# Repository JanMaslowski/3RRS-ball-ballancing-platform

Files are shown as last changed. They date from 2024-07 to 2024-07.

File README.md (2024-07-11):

# 3RRS-ball-ballancing-platform

This repository contains everything needed to create a 3RRS manipulator capable of controlling a ball on a platform using a camera and a PID controller. Programs for the Raspberry Pi 4B are written in Python, and there is also a MATLAB simulation of the model's reverse kinematics. This project was developed as my bachelor thesis and successfully defended at WUST in 2024.

Short video of constructed robot : https://youtu.be/mO_4qzWjOGI

<p align="center">
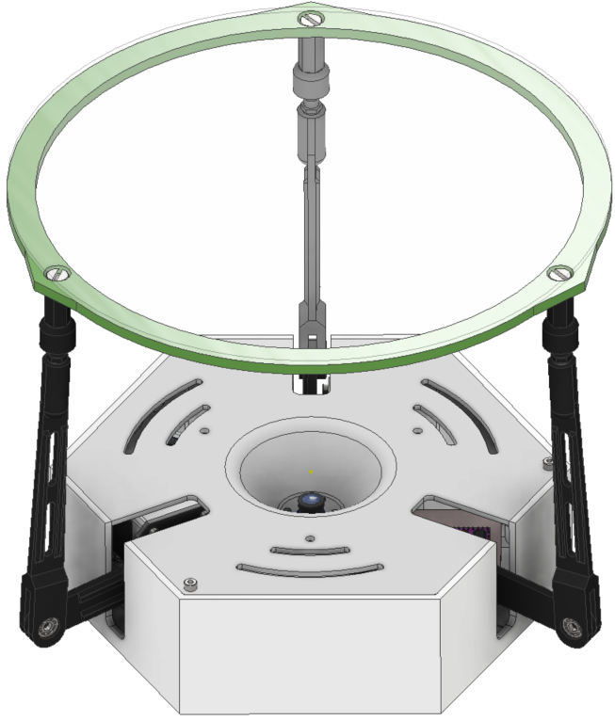
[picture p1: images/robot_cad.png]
Robot CAD
  
</p>

The project shown above was created in Inventor. All files essential for building this robot can be found in the `/inventor_parts_and_model` directory, and the STL files are located in the `/STL_models` directory. Parts that are not included in these directories, such as ball joints or the plexiglass top, were purchased instead of 3D printed. 
On the pictures below you can see parts used to create the robot:

<p align="center">
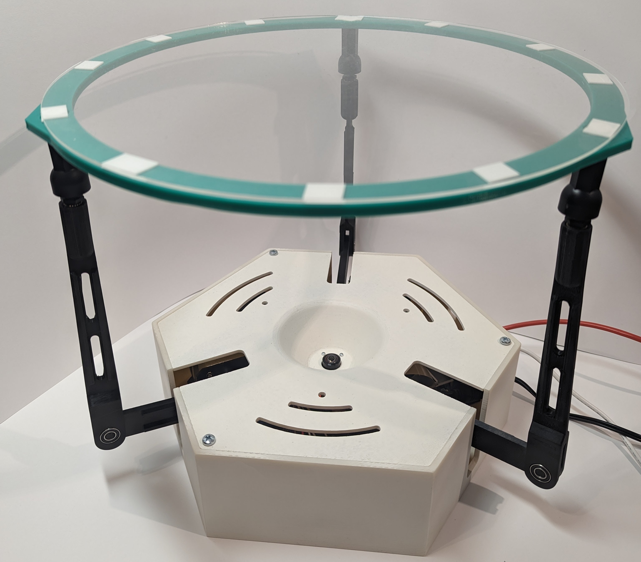
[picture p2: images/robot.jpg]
Robot CAD
  
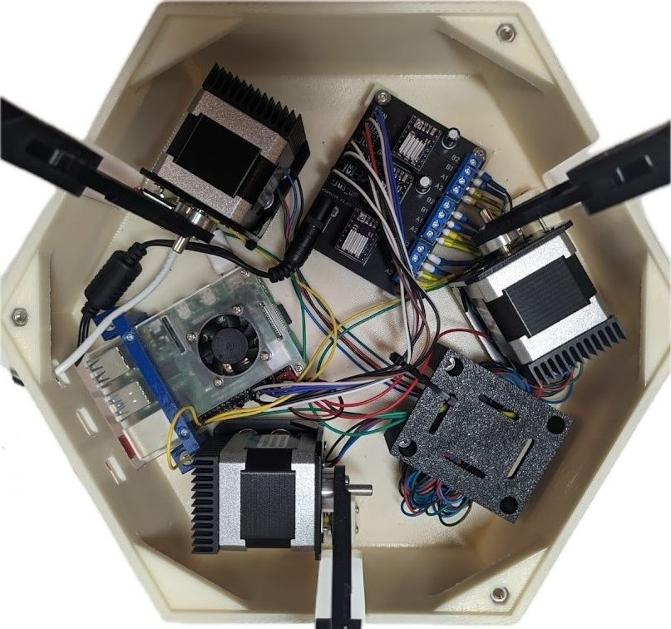
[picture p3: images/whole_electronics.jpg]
Another Image
  
</p>

- Raspberry pi 4b 8GB RAM
- DRV8825 stepper motor driver
- JK42HS40-0404 200 steps 12V/0,4A/0,4Nm stepper motor
- HD M OV5647 5Mpx Camera (fisheye lens)

 PCB board was designed for this project, and its schematic can be found in the `images` directory.

## Matlab simulation

The `simulation.m` file contains a visualization of the platform's circular movement. It helps to understand how inverse kinematics works by analyzing movements with different parameters.

## Camera calibration

A wide-angle camera was used to lower the construction and set everything inside one box. This caused significant image distortion. To manage this, the `/camera_calibration` directory contains two files. The first one, `calibrate.py`, helps to find the camera matrices needed to undistort images. To find these values, you should take photos of a chessboard and put them into the same directory before running the script. The second file, `undistort.py`, shows the image after the undistortion procedure and should be run with the command `undistort.py image_name`.

<p align="center">
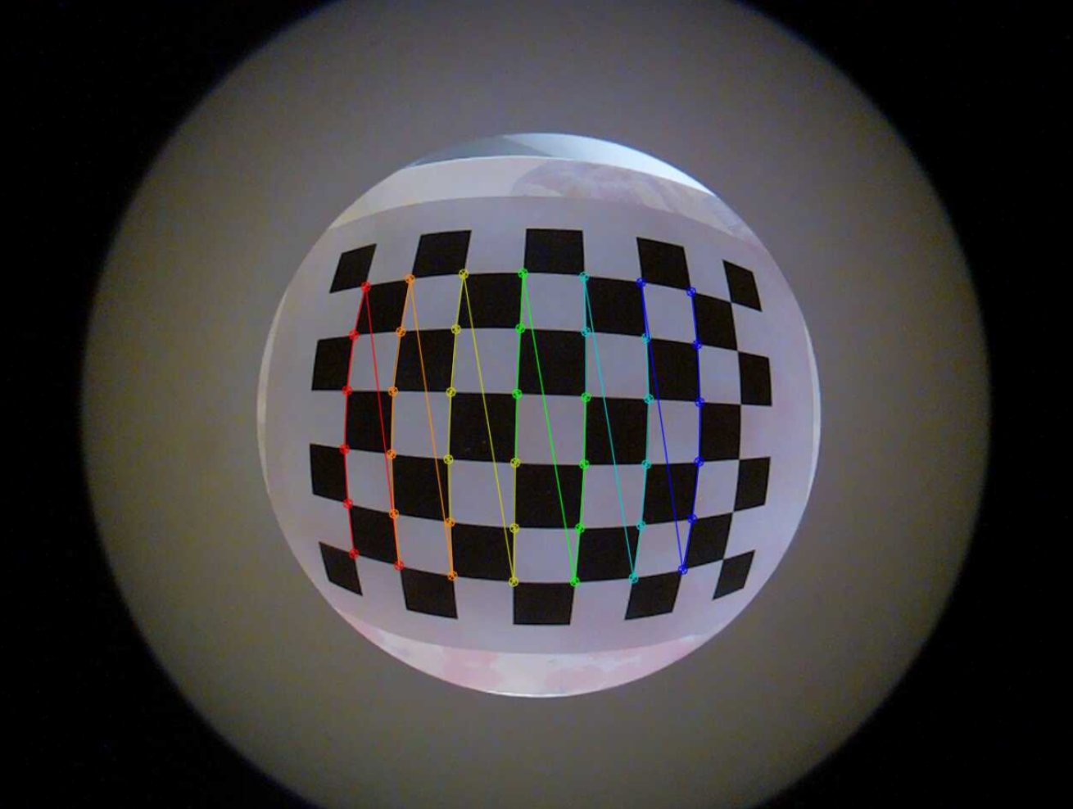
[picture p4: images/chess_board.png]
Robot CA7D
  
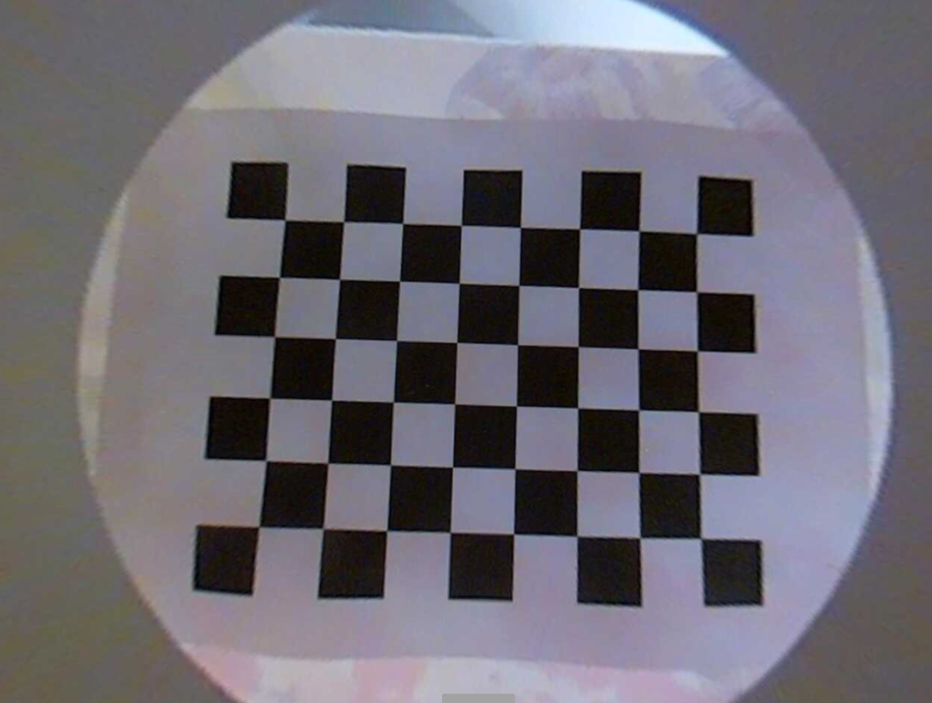
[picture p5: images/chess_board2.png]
Another Ima7ge
  
</p>
Images befor and after camera calibration.

## Scripts

The `scripts` directory contains all the scripts needed to run the platform. Each file is responsible for different functions, which are composed in the `main.py` function.

- `calc.py` is responsible for calculating the inverse kinematics of the manipulator.
- `camera.py` handles all detection tasks, such as finding the ball or the center of the platform. These functionalities are shown in the pictures below.

<p align="center">
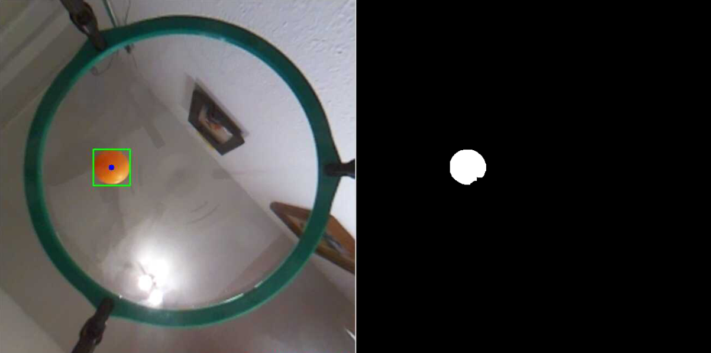
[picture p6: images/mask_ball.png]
Ball Detection
  
</p>

<p align="center">
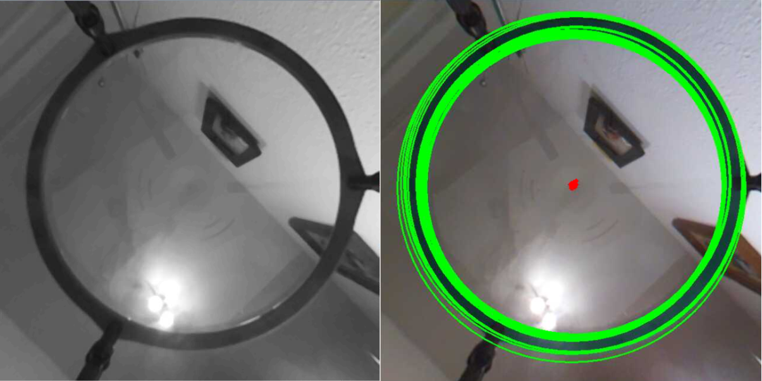
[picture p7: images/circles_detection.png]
Platform Center Detection
  
</p>

- `move32.py` manages all robot movements, such as setting the ground position parallel to the base and reating for ball movement.
- `pid.py` contains the PID regulator algorithm.
- `main.py` sets everything up and runs the program. To see a live view of the camera, as shown below, you should run `main.py --show-trajectory`.

<p align="center">
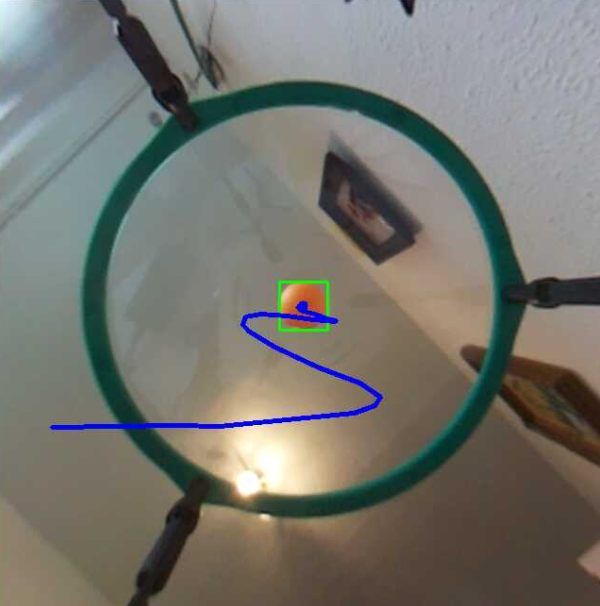
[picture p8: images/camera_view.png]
Camera View
  
</p>

## Other information

Because of the fisheye lens and significant image distortion, the Raspberry Pi 4B 8GB manages to run the program at about 15 frames per second. To increase FPS, ARM NEON and ARM VFPV3 technologies were used. For projects of this kind, you should consider using at least a Raspberry Pi 5 if a fisheye lens is used. It is also likely that this program can be optimized for better performance.

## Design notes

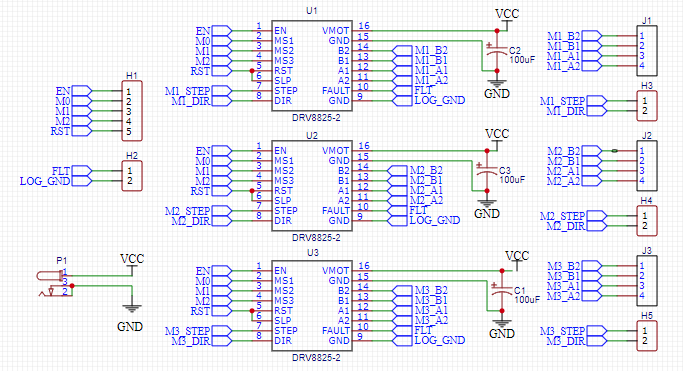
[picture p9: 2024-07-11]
images/pcb_project.png

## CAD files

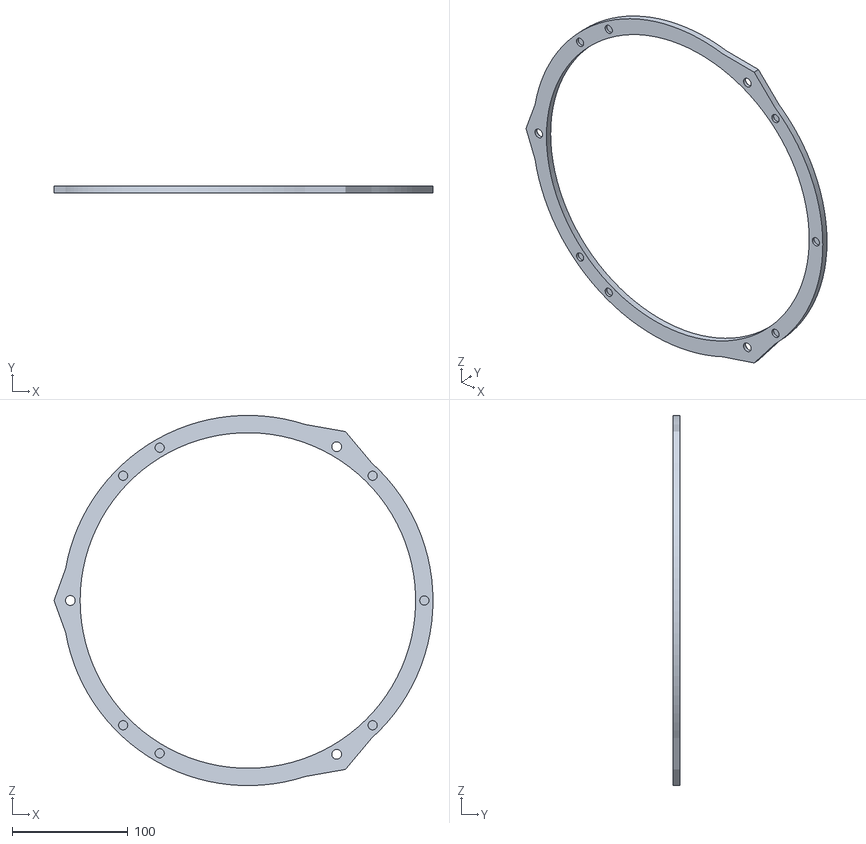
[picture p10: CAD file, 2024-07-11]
STL_models/top.stl
327.6 x 6.00 x 319.9

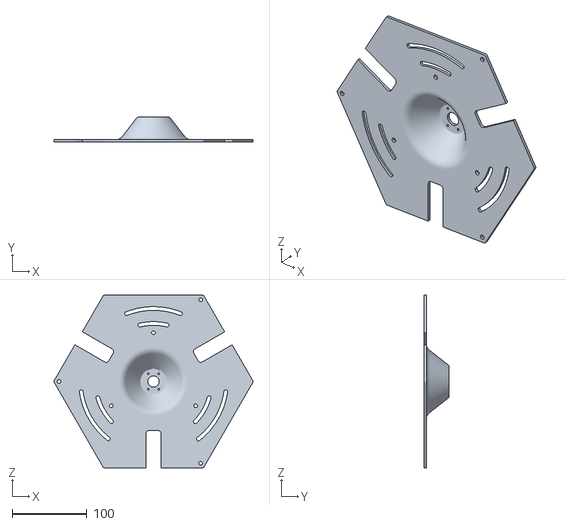
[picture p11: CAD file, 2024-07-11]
STL_models/base_cover.stl
265.8 x 33.0 x 231.0

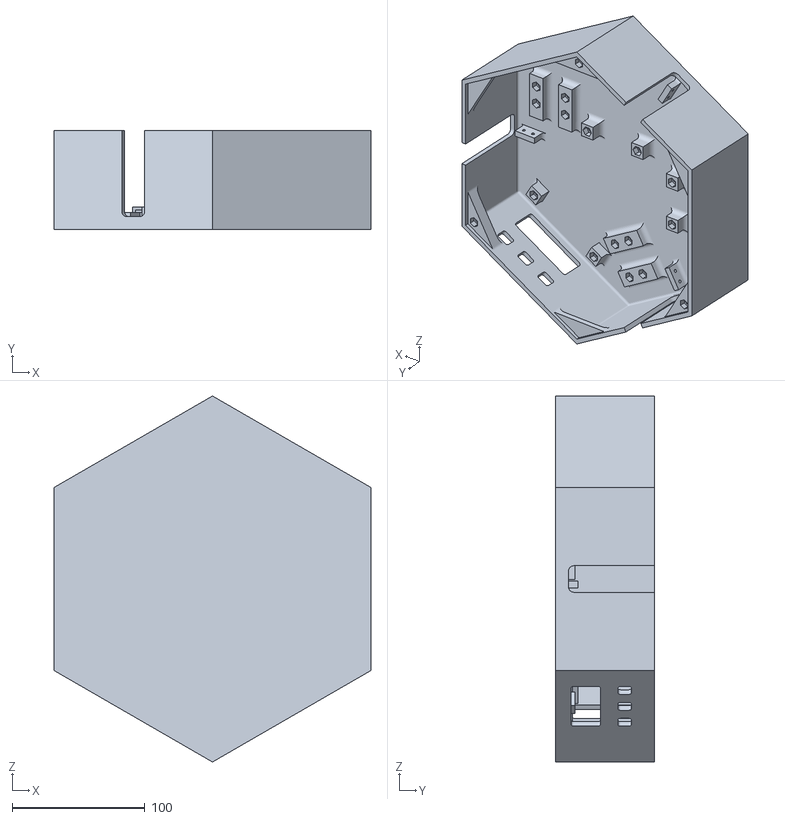
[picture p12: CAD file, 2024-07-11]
STL_models/base_bottom.stl
239.0 x 75.0 x 276.0

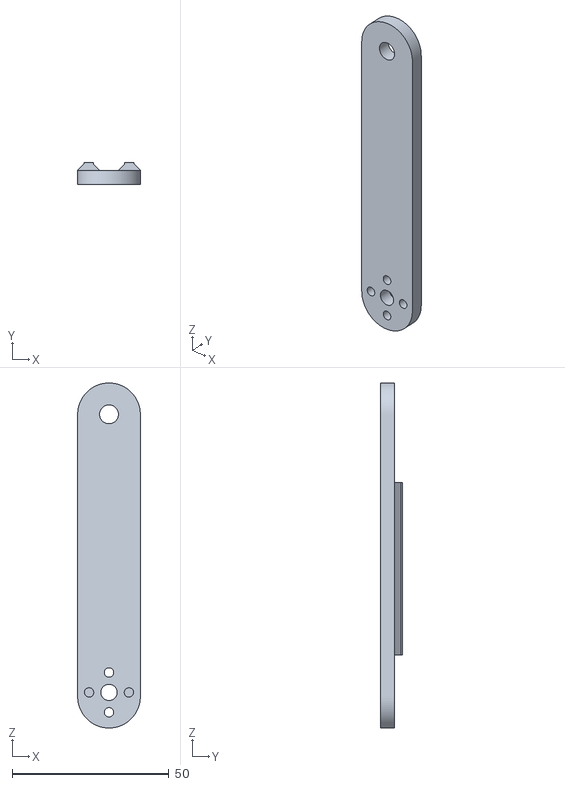
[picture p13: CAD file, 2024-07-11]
STL_models/link_1.stl
20.0 x 7.00 x 110.0

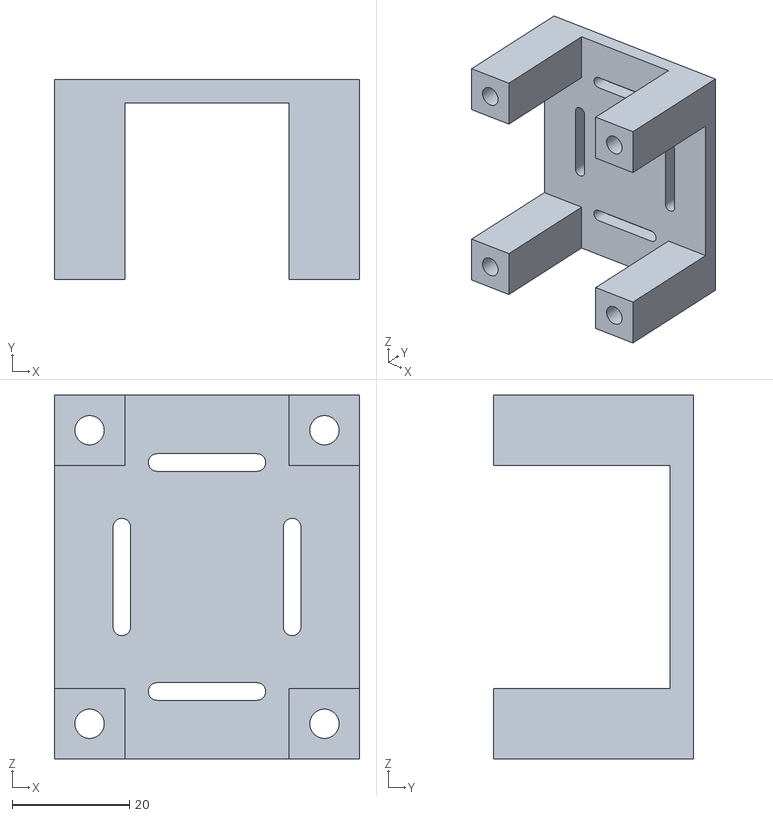
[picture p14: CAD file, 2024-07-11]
STL_models/wires_organiser.stl
52.0 x 34.0 x 62.0

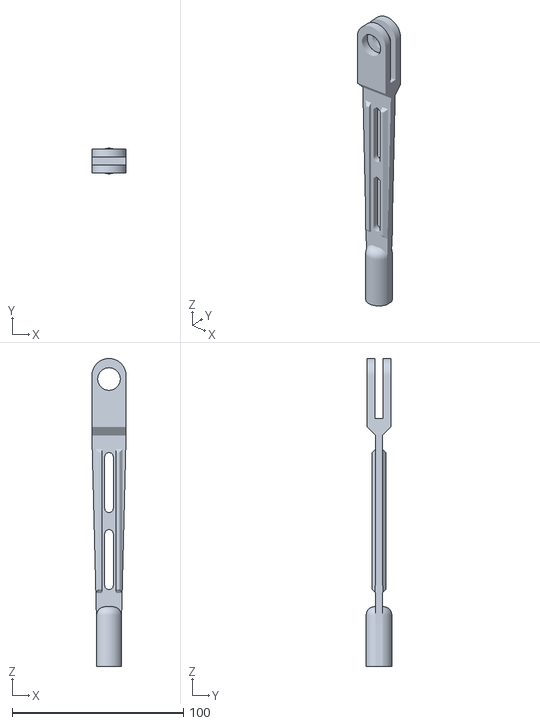
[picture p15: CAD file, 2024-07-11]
STL_models/link_2.stl
20.0 x 15.0 x 180.0

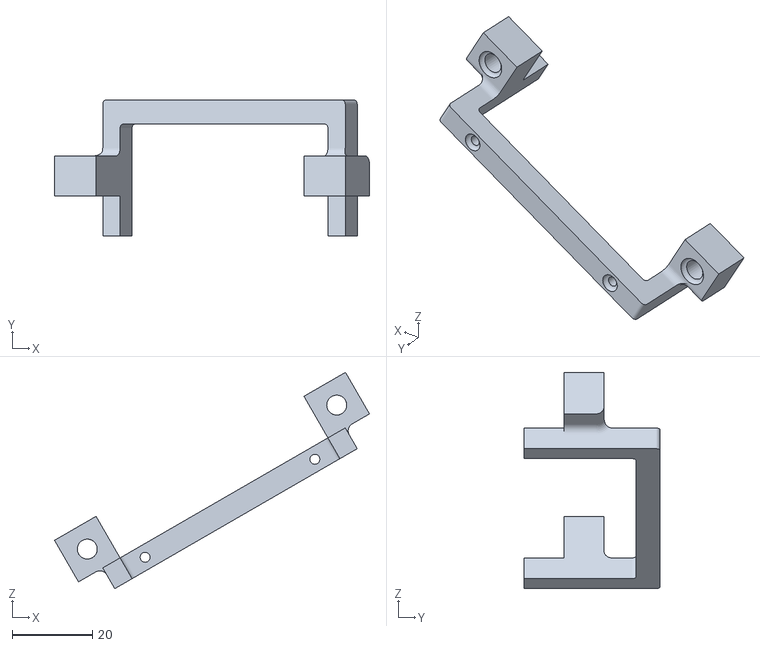
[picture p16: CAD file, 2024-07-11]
STL_models/rpi_handler.stl
78.7 x 34.0 x 54.1

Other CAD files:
iventor_parts_and_model/base_bottom.ipt
iventor_parts_and_model/base_cover.ipt
iventor_parts_and_model/link_1.ipt
iventor_parts_and_model/link_2.ipt
iventor_parts_and_model/rpi_handler.ipt
iventor_parts_and_model/top.ipt
iventor_parts_and_model/wires_organiser.ipt

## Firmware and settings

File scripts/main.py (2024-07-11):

import RPi.GPIO as GPIO
import cv2
import numpy as np
import time
import threading
from picamera2 import Picamera2
import queue
from concurrent.futures import ThreadPoolExecutor
from scipy.interpolate import interp1d
import math

# Import custom modules
from calc import calculate_motor_angles
from camera import correct_pic, detect_circles, detect_orange_ball, correct_center
from move32 import threads_pool_move, multi_get_ground_position
from pid import PID, check_distance_flag

# Camera calibration parameters
DIM = (1280, 972)
K = np.array([[328.57988968885235, 0.0, 640.7563153198729], [0.0, 328.97666546524516, 487.1287892854078], [0.0, 0.0, 1.0]])
D = np.array([[-0.029109933568421023], [0.03052429657029856], [-0.02629029569947379], [0.006725228609111244]])

# Initialize undistort rectify map
map1, map2 = cv2.fisheye.initUndistortRectifyMap(K, D, np.eye(3), K, DIM, cv2.CV_16SC2)

# Initialize camera
picam2 = Picamera2()
picam2.preview_configuration.main.size = (1280, 972)
picam2.preview_configuration.main.format = "RGB888"
picam2.preview_configuration.align()
picam2.configure("preview")
picam2.start()

# Perform initial platform alignment
multi_get_ground_position()
initial_picture = picam2.capture_array()
corrected_initial_pic = correct_pic(initial_picture, map1, map2)
_, const_plat_center_x, const_plat_center_y = detect_circles(corrected_initial_pic)

# PID and motion control parameters
previous_error_x = 0
previous_error_y = 0
iteration_time = 0.006
pid_x = 0
pid_y = 0
current_x_rot = 0
current_y_rot = 0
flagx = 0
flagy = 0
trajectory = []

# Main control loop
def main(show_trajectory_window=True):
    global previous_error_x, previous_error_y, iteration_time, pid_x, pid_y, current_x_rot, current_y_rot, flagx, flagy

    while True:
        start_time = time.time()

        # Capture and correct image
        image = picam2.capture_array()
        corrected_img = correct_pic(image, map1, map2)

        # Detect orange ball
        corrected_img, ball_center_x, ball_center_y = detect_orange_ball(corrected_img, trajectory, 50)

        # Correct platform center
        platform_center = correct_center(const_plat_center_x, const_plat_center_y, current_x_rot, current_y_rot)

        # Calculate offsets
        offset_x = ball_center_x - platform_center[0]
        offset_y = ball_center_y - platform_center[1]
        print("Offsets from center:", offset_x, offset_y)

        # PID control
        if abs(offset_x) < 180 and abs(offset_y) < 180:
            pid_x = PID(offset_x, previous_error_x, iteration_time, flagx)
            pid_y = PID(offset_y, previous_error_y, iteration_time, flagy)
            flagx, flagy = 1, 1
        else:
            flagx, flagy = 0, 0

        # Move motors
        threads_pool_move(pid_y, -pid_x, 0.2)

        # Update iteration time and errors
        iteration_time = time.time() - start_time
        previous_error_x = offset_x
        previous_error_y = offset_y

        # Display trajectory if enabled
        if show_trajectory_window:
            cv2.imshow('Trajectory', corrected_img)

        if cv2.waitKey(1) == ord('q'):
            break

        print("Iteration time:", iteration_time)

    cv2.destroyAllWindows()

if __name__ == "__main__":
    import argparse

    parser = argparse.ArgumentParser(description="Platform control script with optional trajectory window display.")
    parser.add_argument("--show-trajectory", action="store_true", help="Enable to display the trajectory window.")
    args = parser.parse_args()

    main(show_trajectory_window=args.show_trajectory)

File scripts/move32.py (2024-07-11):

# This file contains functions necessary for platform movement

import RPi.GPIO as GPIO
from time import sleep
import threading
from calc import calculate_motor_angles
import queue
from concurrent.futures import ThreadPoolExecutor
import concurrent.futures
from scipy.interpolate import interp1d
from math import sin, cos, radians

# Motion queue
motion_queue = queue.Queue()

############## SETUP PINS 
################################################################
# Pin setup
motor_pins = (7, 8, 14, 15, 23, 24)
resolution_pins = (17, 27, 22)
sensor_pins = (16, 20, 21)
resolution_modes = {
    "1": (0, 0, 0),
    "1/2": (1, 0, 0),
    "1/4": (0, 1, 0),
    "1/8": (1, 1, 0),
    "1/16": (0, 0, 1),
    "1/32": (1, 1, 1)
}

# Motor parameters
# Sensor pin, direction pin, step pin
motor_parameters = {"M1": (16, 15, 14), "M2": (20, 24, 23), "M3": (21, 8, 7)}
# Current angles of the motors
motor_angles = {"M1": 0, "M2": 0, "M3": 0}

# Pin mode setup
GPIO.setmode(GPIO.BCM)

# Sensors
GPIO.setup(sensor_pins, GPIO.IN, pull_up_down=GPIO.PUD_DOWN)

# Motors 
GPIO.setup(motor_pins, GPIO.OUT)
GPIO.setup(resolution_pins, GPIO.OUT)
GPIO.output(resolution_pins, resolution_modes["1/32"])
######################################################################
################### END PIN SETUP

# Function to return the status of a limit switch sensor
# Takes argument:
#   sensor_pin - the sensor pin to check
# Returns:
#   1 if the sensor is pressed, else 0
def sensor_status(sensor_pin):
    while True:
        status = GPIO.input(sensor_pin)
        sleep(0.005)
        return 1 if status == GPIO.HIGH else 0

# Function to return a motor to its zero position until the sensor signal is received
# Takes argument:
#   motor - the motor to move
def get_ground_position(motor):
    GPIO.output(motor_parameters[motor][1], 1)
    while sensor_status(motor_parameters[motor][0]) == 0:
        GPIO.output(motor_parameters[motor][2], GPIO.HIGH)
        sleep(0.005)
        GPIO.output(motor_parameters[motor][2], GPIO.LOW)

# Multi-threaded function to return all motors to their zero position
# Takes no arguments
def multi_get_ground_position():
    motors = ["M1", "M2", "M3"]
    threads = []
    for motor in motors:
        thread = threading.Thread(target=get_ground_position, args=(motor,))
        threads.append(thread)
        thread.start()
    for thread in threads:
        thread.join()
    for motor in motors:
        thread = threading.Thread(target=move_motor, args=(motor, 180, 0.001, 0))
        threads.append(thread)
        thread.start()
    for thread in threads:
        thread.join()
    for motor in motors:
        motor_angles[motor] = 0
    print("Motor angles:", motor_angles)

# Basic function to move motors
# Takes arguments:
#   motor - the motor to move
#   steps - the number of steps to take
#   freq - the frequency (sleep time) with a minimum value of 0.0002
#   direction - direction of movement (0 - up, 1 - down)
# Returns the angle to which the motor has moved relative to the base in degrees
def move_motor(motor, steps, freq, direction):
    GPIO.output(motor_parameters[motor][1], direction)
    for x in range(steps):
        GPIO.output(motor_parameters[motor][2], GPIO.HIGH)
        sleep(freq)
        GPIO.output(motor_parameters[motor][2], GPIO.LOW)
        sleep(freq)
    ang = -1 if direction == 1 else (1 if direction == 0 else None)
    motor_angles[motor] += 0.05625 * steps * ang

# Function to prepare values for movement
# Takes arguments:
#   xrot - rotation angle with respect to the x-axis
#   yrot - rotation angle with respect to the y-axis
#   h - height at which the platform center should be
# Returns a vector of values (number of steps in angles, direction of steps) for each motor
def prepare_motion(xrot, yrot, h):
    M1_angle, M2_angle, M3_angle = calculate_motor_angles(xrot, yrot, h)
    M1_move_diff = motor_angles["M1"] + M1_angle
    M1_dir = 0 if M1_move_diff < 0 else 1
    M2_move_diff = motor_angles["M2"] + M2_angle
    M2_dir = 0 if M2_move_diff < 0 else 1
    M3_move_diff = motor_angles["M3"] + M3_angle
    M3_dir = 0 if M3_move_diff < 0 else 1
    return (abs(M1_move_diff), M1_dir, abs(M2_move_diff), M2_dir, abs(M3_move_diff), M3_dir)

def slow_the_speed(steps):
    freq = 0.000165
    if steps < 10:
        k = interp1d([0, 10], [1.5, 1])
        factor = k(steps)
    else:
        factor = 1
    return freq * factor

# Thread pool function to move motors smoothly
def threads_pool_move(rot_x, rot_y, h):
    with ThreadPoolExecutor(max_workers=3) as executor:
        futures = []
        motion = prepare_motion(rot_x, rot_y, h)
        args_list = [
            ("M1", int(motion[0] * 17.778), slow_the_speed(int(motion[0] * 17.778)), motion[1]),
            ("M2", int(motion[2] * 17.778), slow_the_speed(int(motion[2] * 17.778)), motion[3]),
            ("M3", int(motion[4] * 17.778), slow_the_speed(int(motion[4] * 17.778)), motion[5])
        ]
        for args in args_list:
            future = executor.submit(move_motor_smooth, *args)
            futures.append(future)
        concurrent.futures.wait(futures)
        futures.clear()        

def move_motor_smooth(motor, steps, freq, direction):
    GPIO.output(motor_parameters[motor][1], direction)
    for x in range(steps):
        if x / steps < 0.20:
            m = interp1d([0, steps * 0.20], [1.6, 1])
            GPIO.output(motor_parameters[motor][2], GPIO.HIGH)
            sleep(m(x) * freq)
            GPIO.output(motor_parameters[motor][2], GPIO.LOW)
            sleep(m(x) * freq)
        elif x / steps > 0.8:
            n = interp1d([0.8 * steps, steps], [1, 1.6])
            GPIO.output(motor_parameters[motor][2], GPIO.HIGH)
            sleep(n(x) * freq)
            GPIO.output(motor_parameters[motor][2], GPIO.LOW)
            sleep(n(x) * freq)
        else:
            GPIO.output(motor_parameters[motor][2], GPIO.HIGH)
            sleep(freq)
            GPIO.output(motor_parameters[motor][2], GPIO.LOW)
            sleep(freq)
    ang = -1 if direction == 1 else (1 if direction == 0 else None)
    motor_angles[motor] += 0.05625 * steps * ang

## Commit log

2024-07-11 Added files to 3D print
    [base_bottom.stl, base_cover.stl, link_1.stl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]
2024-07-11 Inventor23 model and parts that were 3D printed
    [base_bottom.ipt, base_cover.ipt, link_1.ipt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]
2024-07-11 Scripts for fisheye lens calibration
